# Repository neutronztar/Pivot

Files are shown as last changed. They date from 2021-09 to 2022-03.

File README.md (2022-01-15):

# Pivot
Pivot is an open source robotic art piece similar to Mark Setrakian's [Axis 1 and 2](https://www.youtube.com/watch?v=NsFBHqbNKvA&t=72s). Here is [a video](https://youtu.be/PGe4sWHx0f0) about how I designed and built it

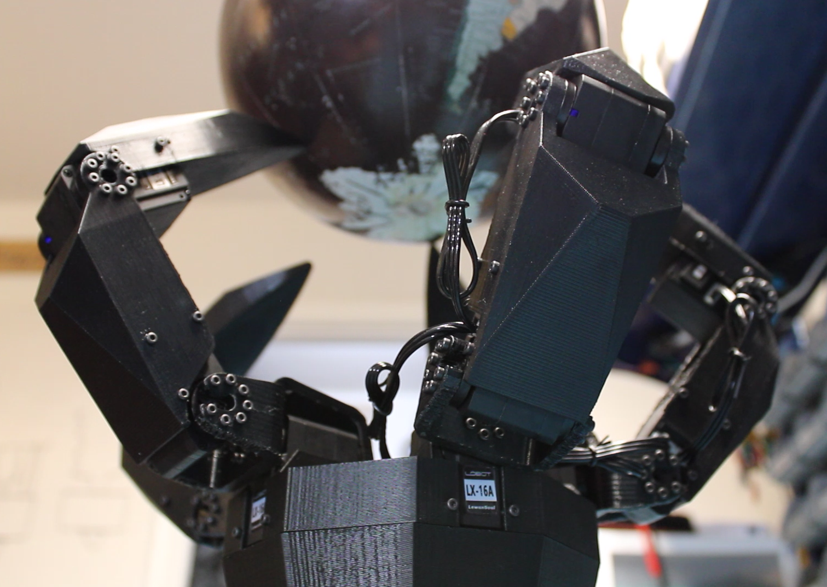
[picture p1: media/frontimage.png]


## Bill of Materials
### General Parts
| Part | Quantity | Approx Price | Total | Notes |
|---|---|---|---|---|
| [LX-16A Servo](https://smile.amazon.com/gp/product/B073XY5NT1/ref=ppx_yo_dt_b_search_asin_title?ie=UTF8&psc=1) | 15 | $20 | $300 | You also need the wires and plastic mounting rings that come with these.
| [JoyStick](https://smile.amazon.com/dp/B08CGYGMJL?psc=1&ref=ppx_yo2_dt_b_product_details) | 1 | $21 | $21 |
| [2 x 0.4 x 8 mm Machine Screws](https://www.boltdepot.com/Metric_socket_cap_Class_12.9_alloy_steel_black_oxide_finish_2mm_x_0.4mm.aspx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) | 400 | $0.0946 | $38 | Exact qty is 300, but you should get some extra. |
| [12V Power Supply](https://www.ebay.com/itm/153588427332) | 1 | $7 | $7 |
| [AC Power Connector](https://smile.amazon.com/dp/B00H8QL53A?psc=1&ref=ppx_yo2_dt_b_product_details) | 1 | $7 | $7 |
| [PETG Filament](https://smile.amazon.com/gp/product/B07PGYHYV8/ref=ppx_yo_dt_b_search_asin_title?ie=UTF8&psc=1) | 1kg | $23 | $23 |  |
| [Plaster of Paris](https://smile.amazon.com/Dap-Plaster-Paris-20-Min/dp/B008SR3W1G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) | 1 | $10 | $10 |  |
| [Round Power Switch](https://www.ebay.com/itm/203485577266?hash=item2f60af8032:g:Sh4AAOSwmDtgvNwT) | 1 | $3 | $3 |  |
| [Power Connector](https://smile.amazon.com/gp/product/B07DCXKNXQ/ref=ppx_yo_dt_b_search_asin_title?ie=UTF8&psc=1) | 1 | $7 | $7 |  |

### PCB Parts
| Part | Quantity | Approx Price | Total | Notes |
|---|---|---|---|---|
| [ESP32 DevKit](https://smile.amazon.com/gp/product/B086MLNH7N/ref=ppx_yo_dt_b_search_asin_title?ie=UTF8&psc=1) | 1 | $7 | $7 |
| [8V Buck Converter](https://smile.amazon.com/dp/B07BDDMGLG?ref=ppx_yo2_dt_b_product_details&th=1) | 1 | $7 | $7 |
| [5V Buck Converter](https://smile.amazon.com/gp/product/B01MQGMOKI/ref=ppx_yo_dt_b_search_asin_title?ie=UTF8&th=1) | 1 | $11 | $11 |
| [Molex Spox 3pin Connectors](https://www.mouser.com/ProductDetail/Molex/35301-0340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) | 5 | $0.26 | $1.30 | |
| [1000uF Electrolytic Cap](https://smile.amazon.com/dp/B06XRDWF5X?psc=1&ref=ppx_yo2_dt_b_product_details) | 4 |  | $15 |  |
| [10uF Electrolytic Cap](https://smile.amazon.com/dp/B06XRDWF5X?psc=1&ref=ppx_yo2_dt_b_product_details) | 1 | |  |  |
| [Tri-State Buffer: SN74LS241N](https://smile.amazon.com/gp/product/B08FZVPJD9/ref=ppx_yo_dt_b_search_asin_title?ie=UTF8&psc=1) | 1 | $9 | $9 |  |
| Logic Level Shifter SMD: TXS0108EPWR | 1 | |  | JLC |
| 1k Resistor SMD: 0603WAF1001T5E | 1 |  |  | JLC |
| 10k Resistor SMD: 0603WAF1002T5E | 1 |  |  | JLC |
| 100nF Cap SMD: CC0603KRX7R9BB104 | 2 |  |  | JLC |

### 3D Printed Parts
| Part | Quantity |
|---|---|
| tip.STL | 5 |
| fingerA.STL | 5 |
| knuckle.STL | 5 |
| palm.STL | 1 |
| mid.STL | 1 |
| base.STL | 1 |

#### Approximate Grand Total: $466

## The Code
To make this machine do its magic, every ".py" file in the root of the "MicroPython" directory must be uploaded to the ESP32. I used the utility ["rshell"](https://pypi.org/project/rshell/) to do this. Also the ESP32 must first be loaded with a [MicroPython binary](https://micropython.org/download/esp32/) (tested on v1.17).

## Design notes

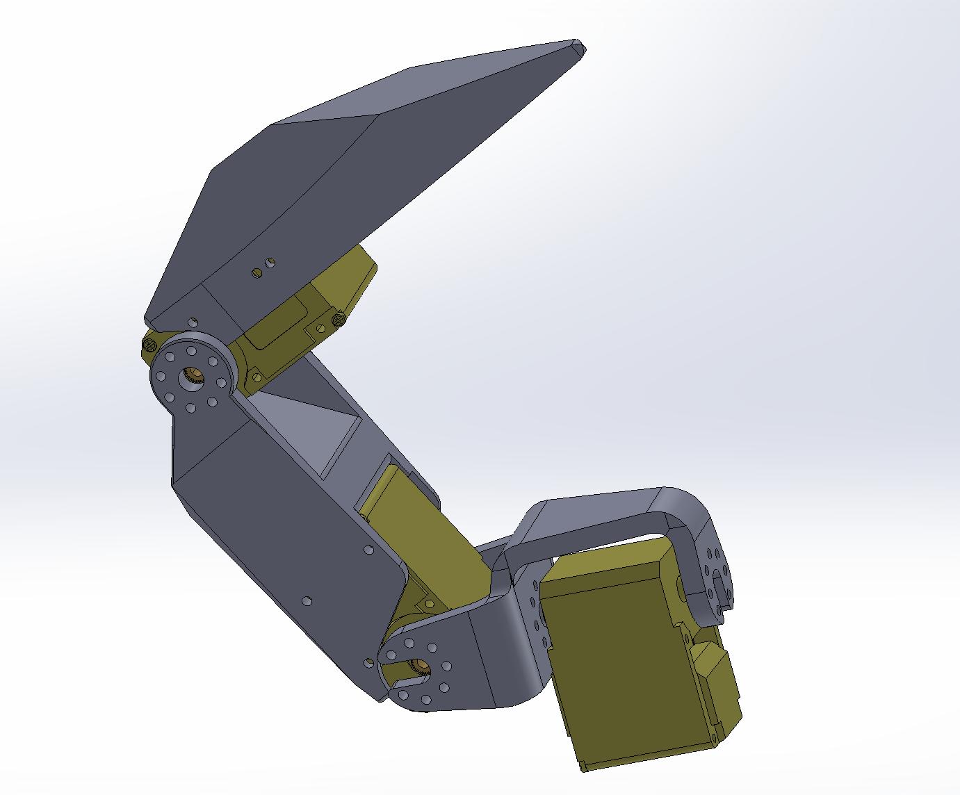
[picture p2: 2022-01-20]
media/sw_finger.jpeg

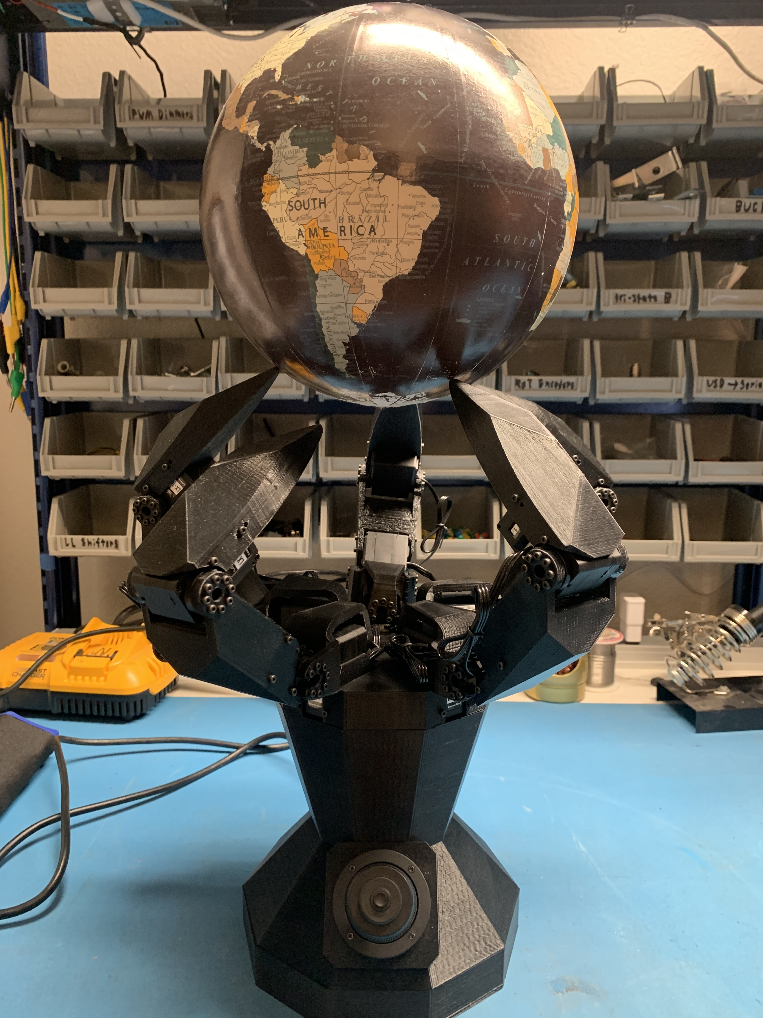
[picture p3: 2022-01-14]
media/verticalpic.jpeg

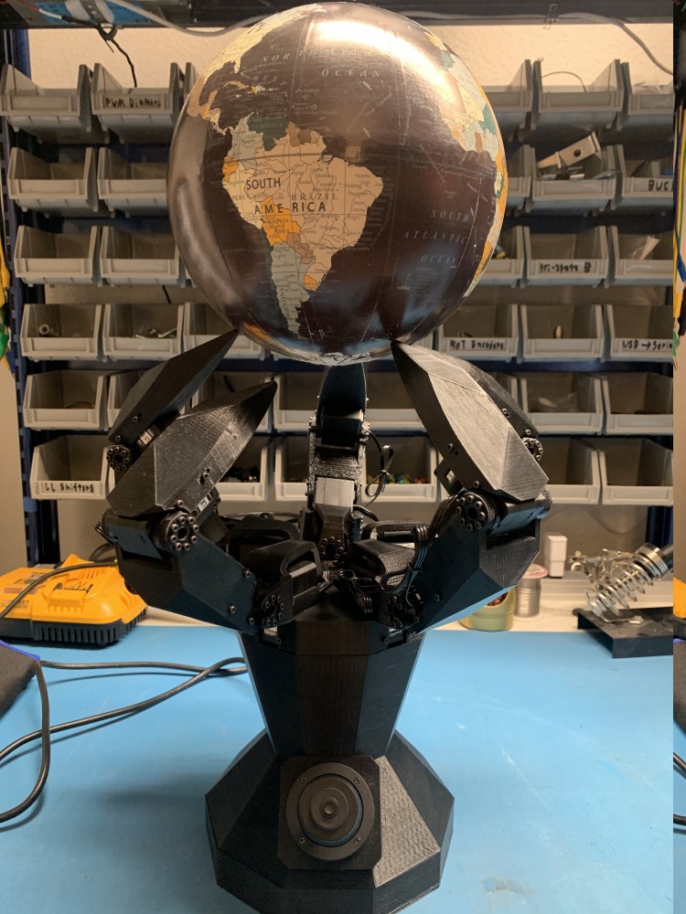
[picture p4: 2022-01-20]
media/verticalpicsmaller.jpeg

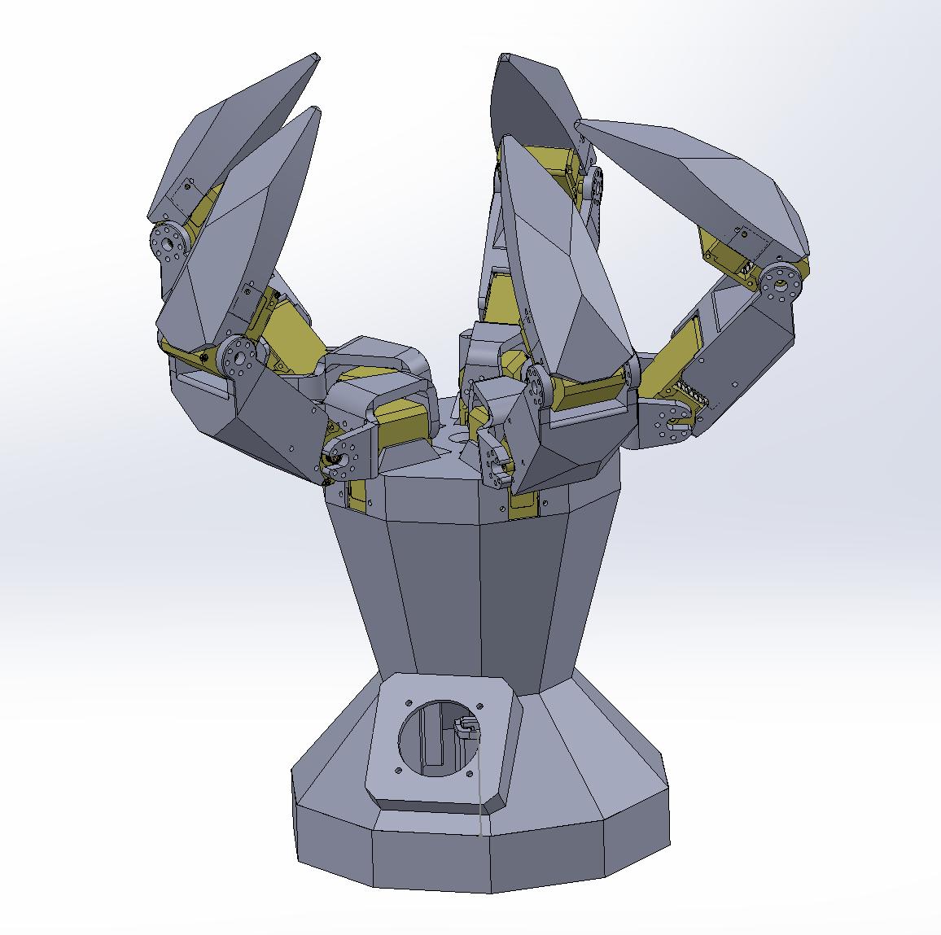
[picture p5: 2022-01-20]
media/sw.jpeg

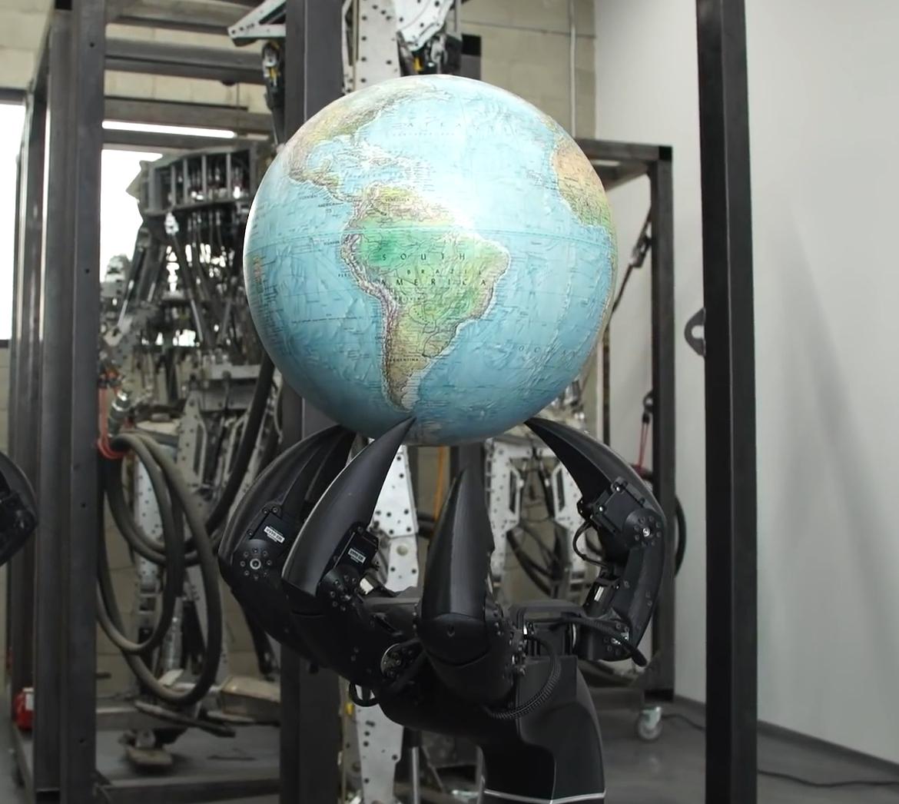
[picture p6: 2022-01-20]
media/axis.jpeg

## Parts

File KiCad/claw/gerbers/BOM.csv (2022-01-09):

Comment | Designator | Footprint | LCSC Part Number
1k | R1 | 0603 | C21190
10k | R2 | 0603 | C25804
100nF | C1,C2 | 0603 | C14663
TXS0108EPWR | U2 | TSSOP-20_4.4x6.5x0.65P | C17206

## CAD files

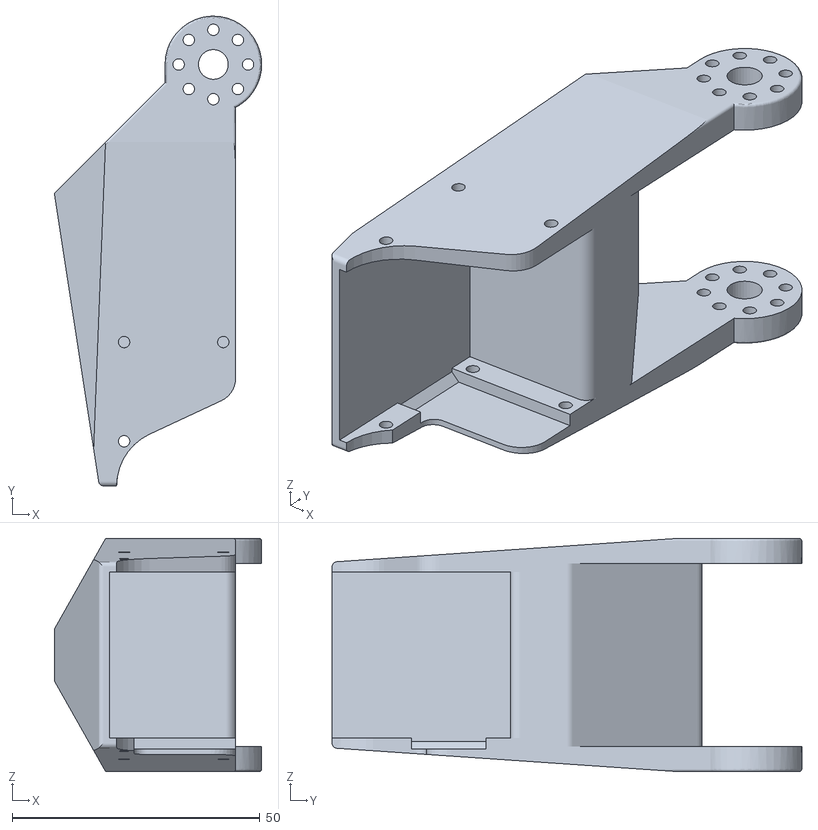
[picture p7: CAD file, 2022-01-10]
3Dmodels/fingerA.STL
41.8 x 94.7 x 47.0

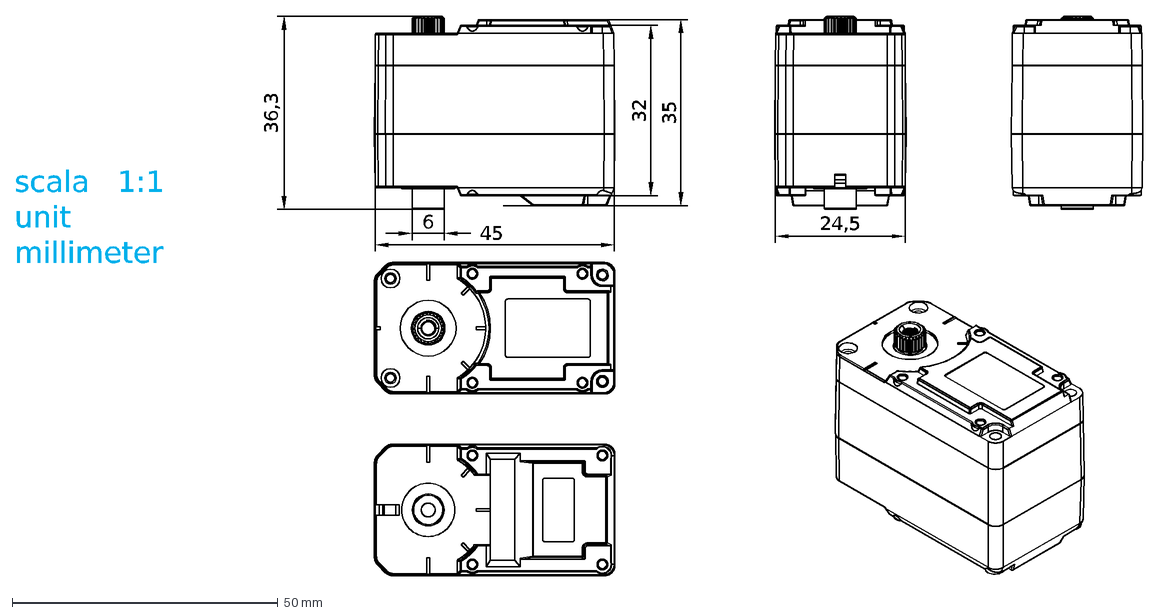
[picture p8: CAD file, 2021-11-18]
LX-16A/LX-16A.dxf
36,3
45
35
32
24,5
6
scala 1:1 unit millimeter

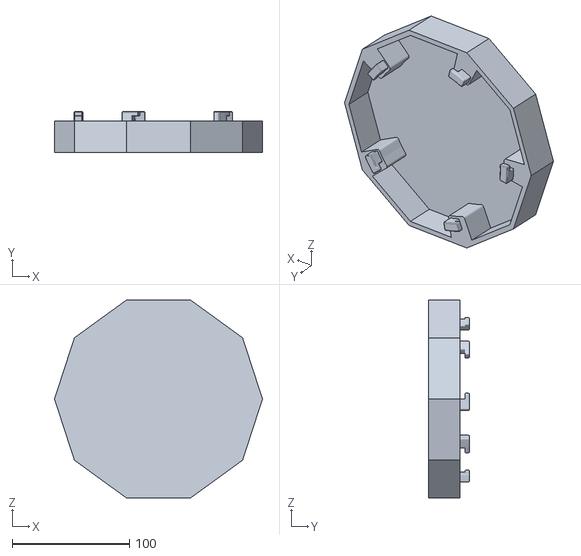
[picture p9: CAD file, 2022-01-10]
3Dmodels/base.STL
177.4 x 35.0 x 168.7

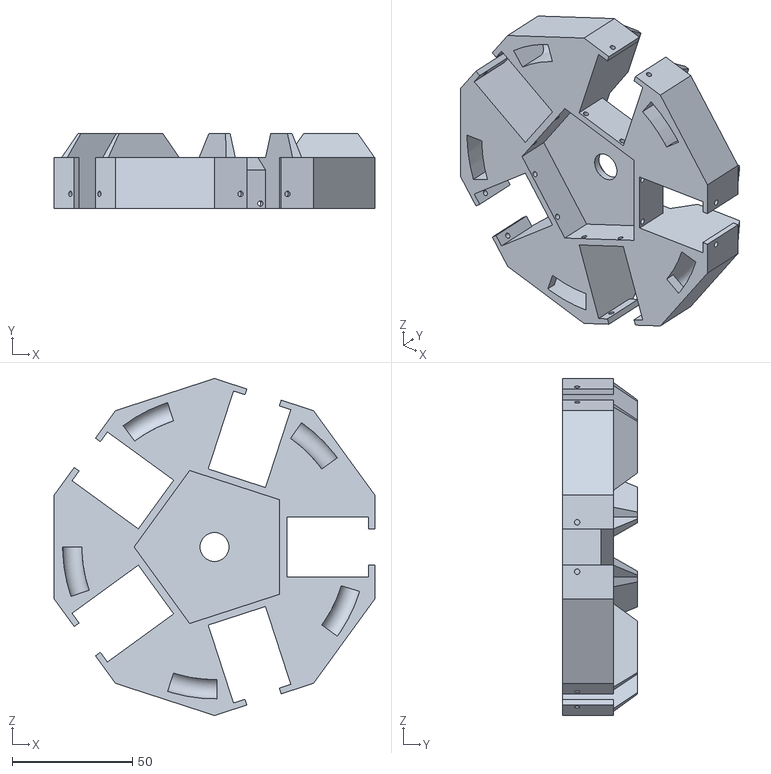
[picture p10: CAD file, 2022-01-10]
3Dmodels/palm.STL
133.0 x 31.0 x 139.8

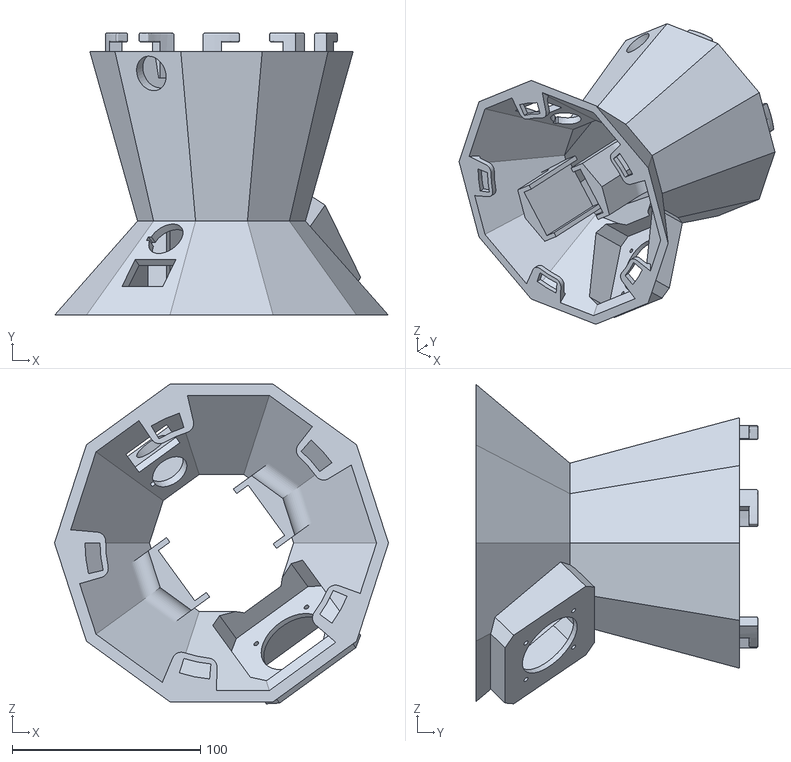
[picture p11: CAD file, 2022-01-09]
3Dmodels/mid.STL
177.4 x 150.0 x 169.8

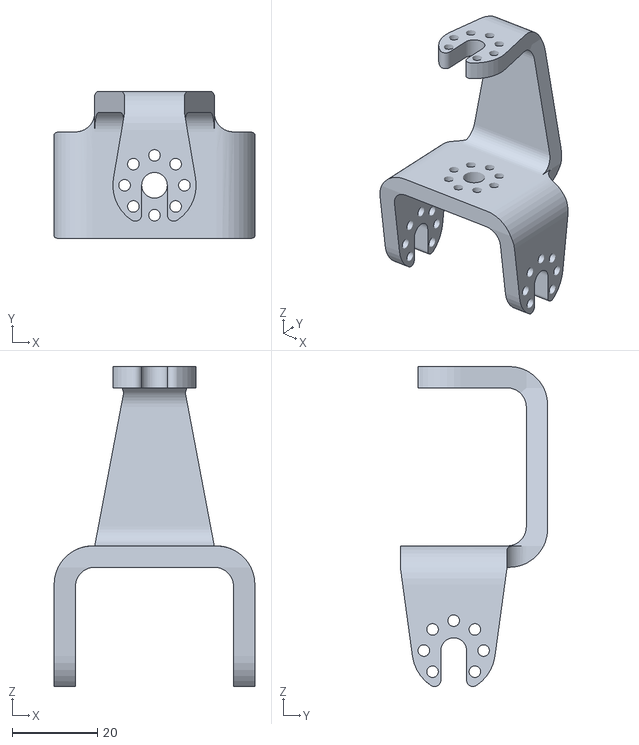
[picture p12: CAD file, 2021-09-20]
3Dmodels/knuckle.STL
47.0 x 34.5 x 74.9

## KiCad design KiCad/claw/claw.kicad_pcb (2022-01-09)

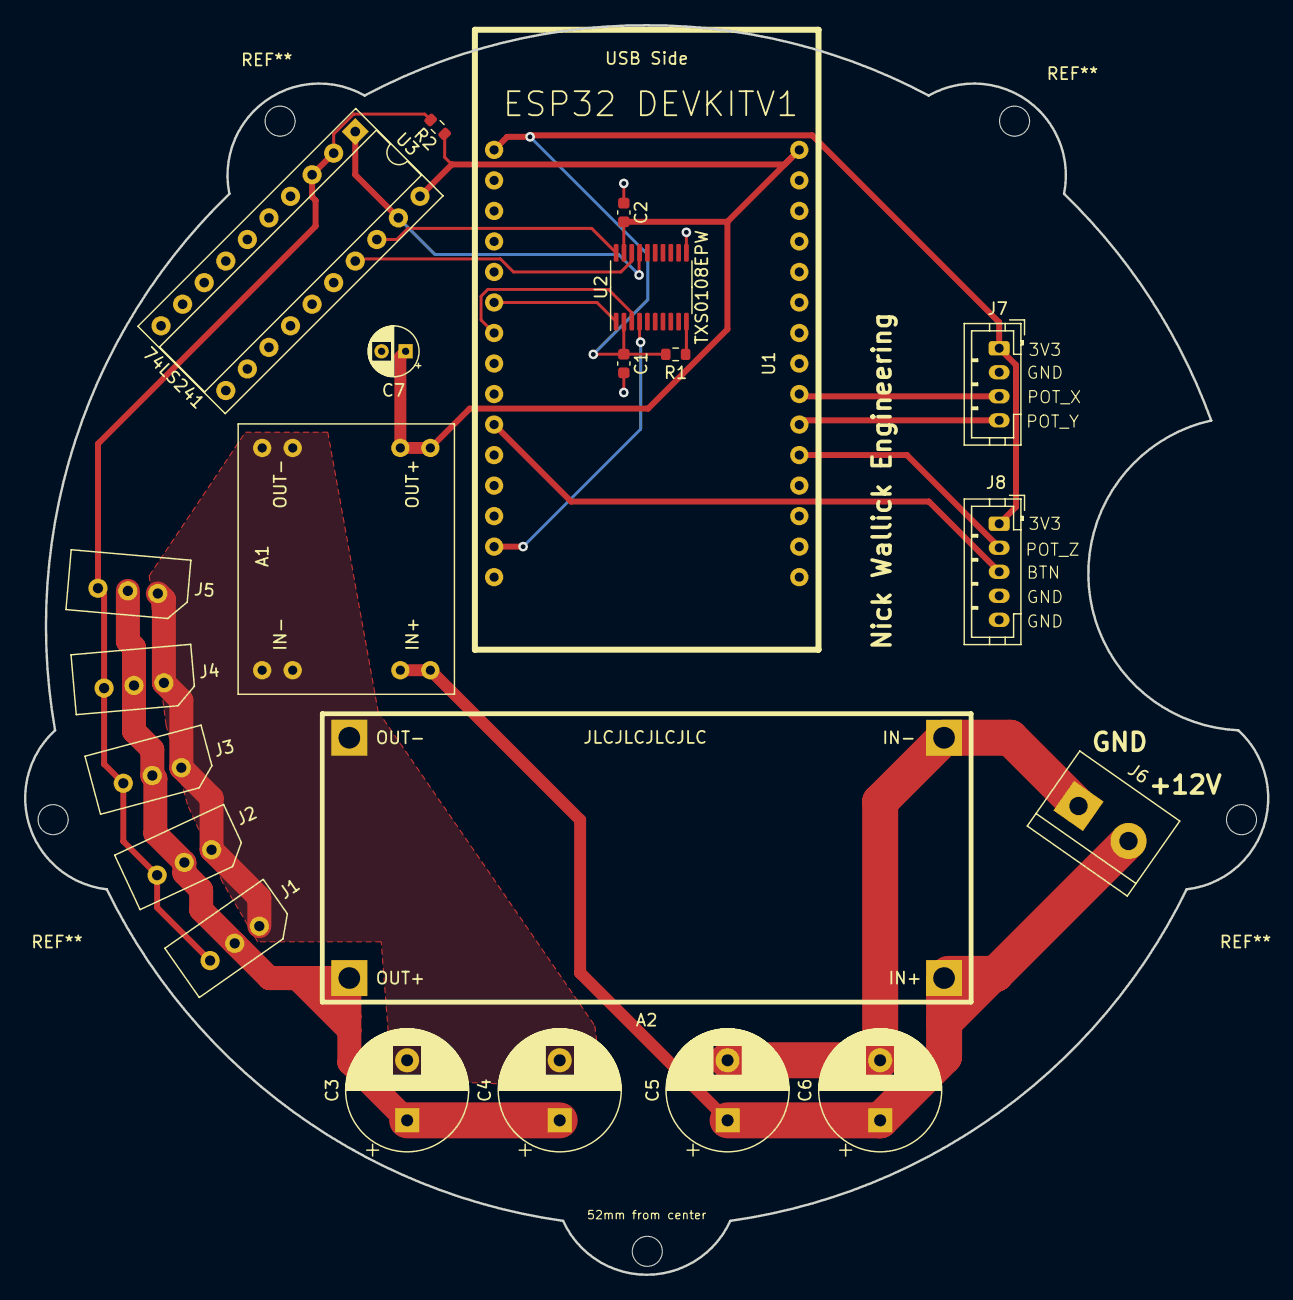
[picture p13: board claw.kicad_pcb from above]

Board: 2 copper layers, 103.5 x 104.0 mm, 22 parts (0 on the bottom side), 17 nets.

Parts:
A1: DC-DC_Buck; MP1584EN_DC-DC_Buck
A2: DC-DC_Buck; DZS_Elec_DC-DC_Buck
C1, C2: 100nF; C_0603_1608Metric
C3, C4, C5, C6: 1000u; CP_Radial_D10.0mm_P5.00mm
C7: 10u; CP_Radial_D4.0mm_P2.00mm
J1, J2, J3, J4, J5: Molex_Spox_3pin; Molex_Spox_3Pin_2.5mmPitch
J6: Screw_Terminal_01x02; TerminalBlock_bornier-2_P5.08mm
J7: Conn_01x04_Male; JST_PH_B4B-PH-K_1x04_P2.00mm_Vertical
J8: Conn_01x05_Male; JST_PH_B5B-PH-K_1x05_P2.00mm_Vertical
R1: 1k; R_0603_1608Metric
R2: 10k; R_0603_1608Metric
U1: ESP32_DEVKITV1
U2: TXS0108EPW; TSSOP-20_4.4x6.5mm_P0.65mm
U3: 74LS241; DIP-20_W7.62mm_Socket

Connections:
+3V3: C1.1, J7.1, J8.1, R1.1, U1.1, U2.2
+5V: A1.3, C2.2, C7.1, R2.1, U1.30, U2.19, U3.20
+8V: A2.3, C3.1, C4.1, J1.2, J2.2, J3.2, J4.2, J5.2
+12V: A1.4, A2.4, C5.1, C6.1, J6.2
BUTTON: J8.3, U1.10
DIR_3V3: U1.14, U2.4
DIR_5V: U2.17, U3.1, U3.19
GND: A1.1, A1.2, A2.1, A2.2, C1.2, C2.1, C3.2, C4.2, C5.2, C6.2, C7.2, J1.1, J2.1, J3.1, J4.1, J5.1, J6.1, J7.2, J8.4, J8.5, U1.2, U1.29, U2.11, U3.10
MOTOR_SIGNAL: J1.3, J2.3, J3.3, J4.3, J5.3, R2.2, U3.2, U3.3
unnamed: R1.2, U2.10
POT_X: J7.3, U1.22
POT_Y: J7.4, U1.21
POT_Z: J8.2, U1.20
RX_3V3: U1.6, U2.1
RX_5V: U2.20, U3.18
TX_3V3: U1.7, U2.3
TX_5V: U2.18, U3.17

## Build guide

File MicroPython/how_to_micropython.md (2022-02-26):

# MicroPython Commands for Controlling ESP32 on Linux #

## installing mp
cd /home/nick/.local/lib/python3.8/site-packages
python3 esptool.py --chip esp32 --port /dev/ttyUSB0 erase_flash
python3 esptool.py --chip esp32 --port /dev/ttyUSB0 --baud 460800 write_flash -z 0x1000 esp32-20210902-v1.17.bin

## list files on board
ampy -p /dev/ttyUSB0 ls

## control board with REPL
picocom /dev/ttyUSB0 -b115200
then push 'en' button on board
exit picocom with Ctrl-a --> Ctrl-x

## Connect with rshell (broken on MicroPython 1.17... or not?)
rshell -p /dev/ttyUSB0
## Then list files on board
ls /pyboard
## Enter REPL
repl
## Run file from REPL
exec(open('file.py').read())

## MicroPython Tools
ampy rshell mpfshell

## All importable modules
help('modules')

## check ram
import micropython as mp
mp.mem_info(True)

## check file-system space
import os
os.statvfs('/')
https://docs.micropython.org/en/latest/library/os.html#:~:text=file%20or%20directory.-,os.statvfs,-(path)

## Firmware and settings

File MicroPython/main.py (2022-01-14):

import time
from math import isinf, pi
from micropython import const
from machine import ADC, Pin
from claw import Claw, time_it
from constants import *


def main():
    claw = Claw(22)

    # Left and right joystick potentiometer
    potX = ADC(Pin(33))
    potX.atten(ADC.ATTN_11DB)

    # Front and back joystick potentiometer
    potY = ADC(Pin(32))
    potY.atten(ADC.ATTN_11DB)

    # Up and Down joystick potentiometer
    potZ = ADC(Pin(35))
    potZ.atten(ADC.ATTN_11DB)

    # Button on top of joystick
    button = Pin(19, Pin.IN, Pin.PULL_UP)
    button.irq(trigger=Pin.IRQ_RISING, handler=button_callback)
    global buttonPressed
    buttonPressed = False
    mode = 0

    speedTable = {
    # speed:    numFrames
      -12:        -20,       # fastest reverse
      -11:        -25,
      -10:        -30,
       -9:        -35,
       -8:        -40,
       -7:        -45,
       -6:        -50,
       -5:        -55,
       -4:        -60,
       -3:        -65,
       -2:        -70,
       -1:        -75,
        0:        -80,       # slowest reverse
        1:         80,       # slowest
        2:         75,
        3:         70,
        4:         65,
        5:         60,
        6:         55,
        7:         50,
        8:         45,
        9:         40,
        10:        35, 
        11:        30,
        12:        25,
        13:        20        # fastest
    }

    speed = -4
    numFrames = speedTable[speed]
    
    STRIDE = 1.15               # radians, must be less than 2*pi/5
    OFFSET_ANGLE = -STRIDE / 2 + pi / 10  # radians
    FRAME_TIME = const(60)      # ms
    
    center = [0, 0, 150]        # center of the circle that the finger tips move along
    radius = 50
    numFrames = -60
    phase = 0                   # sweeps 0-359
    frameStartTime = time.ticks_ms()
    firstLoop = True


    ### MAIN LOOP ###
    while True:
        # Update values based on user input
        center, radius, speed, mode = update_values(potX, potY, potZ, center, radius, speed, mode)
        numFrames = speedTable[round(speed)]
        
        # Calculate angles of all 15 servos for next frame
        angles = claw.calc_frame_angles(phase, STRIDE, OFFSET_ANGLE, radius, center)

        # ------Wait------
        while time.ticks_diff(time.ticks_ms(), frameStartTime) < FRAME_TIME:
            pass
        frameStartTime = time.ticks_ms() # reset timer
        
        # Move all fingers to frame
        claw.move_to_frame(angles, FRAME_TIME, firstLoop)
        firstLoop = False

        # Increment phase
        phase = (phase + 360 / numFrames) % 360



def update_values(potX, potY, potZ, center, radius, speed, mode):
    """Update values based on user input"""
    
    def bound(val, low, high):
        return max(low, min(high, val))
    

    # Cycle mode if button on top of joystick was pressed
    global buttonPressed
    if buttonPressed == True:
        mode = (mode + 1) % 3
        buttonPressed = False

    # Read all POTs
    joyX = potX.read() - X_AVG
    joyY = potY.read() - Y_AVG
    joyZ = potZ.read() - Z_AVG


    # Map XY joystick movement to XY globe movement
    if joyX > SLOP:
        targetX = int(min(joyX - SLOP, 1200) * 50/1200)
    elif joyX < -SLOP:
        targetX = int(max(joyX + SLOP, -1200) * 50/1200)
    else:
        targetX = 0

    if joyY > SLOP:
        targetY = int(min(joyY - SLOP, 1200) * 50/1200)
    elif joyY < -SLOP:
        targetY = int(max(joyY + SLOP, -1200) * 50/1200)
    else:
        targetY = 0

    xStep = int((targetX - center[0]) / 4)
    yStep = int((targetY - center[1]) / 4)
   
    center[0] += xStep
    center[1] += yStep

    
    if mode == 0:

        # Map spinning joystick to Z globe movement
        if joyZ > SLOP:
            zStep = int(min(joyZ - SLOP, 1200) * 6/1200)
        elif joyZ < -SLOP:
            zStep = int(max(joyZ + SLOP, -1200) * 6/1200)
        else:
            zStep = 0

        center[2] = bound(center[2] + zStep, 100, 180)
    
    elif mode == 1:

        # Map spinning joystick to radius
        if joyZ > SLOP:
            rStep = int(min(joyZ - SLOP, 1200) * 4/1200)
        elif joyZ < -SLOP:
            rStep = int(max(joyZ + SLOP, -1200) * 4/1200)
        else:
            rStep = 0
        
        radius = bound(radius + rStep, 20, 80)
    
    elif mode == 2:

        # Map spinning joystick to speed
        if joyZ > SLOP:
            speed = bound(speed - 0.2, -12, 13)
        elif joyZ < -SLOP:
            speed = bound(speed + 0.2, -12, 13)


    return center, radius, speed, mode


def button_callback(p):
    global buttonPressed
    buttonPressed = True


if __name__ == "__main__":
    main()

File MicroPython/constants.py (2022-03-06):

from math import radians, sin, cos
from micropython import const


# Distance from center of palm to axis 1 for each finger
D = (91, 91, 91, 91, 91)

# Angle from X-axis for each finger
THETA_DEG = (18, 90, 162, 234, 306)
THETA = tuple(map(radians, THETA_DEG))

# Vector for each of the finger start positions
D_VECT = (
    (D[0]*cos(THETA[0]), D[0]*sin(THETA[0]), 0),
    (D[1]*cos(THETA[1]), D[1]*sin(THETA[1]), 0),
    (D[2]*cos(THETA[2]), D[2]*sin(THETA[2]), 0),
    (D[3]*cos(THETA[3]), D[3]*sin(THETA[3]), 0),
    (D[4]*cos(THETA[4]), D[4]*sin(THETA[4]), 0)
)

# Lengths (mm)
FINGER_LEN = const(85) # exact: 85.38
TIP_LEN = const(118)   # exact: 118.04

# Motor IDs (knuckle,finger,tip) for each finger
MOTOR_ID = ((0,1,2), (3,4,5), (6,7,8), (9,10,11), (12,13,14))

# Offest Angles (knuckle,finger,tip) for each finger
OFFSET_ANGLE = ((-1,-2,9), (1,-2,9), (-1,-6,9), (1,-4,6), (-1,-6,10))

# Motor angle limits - limits move with the offsets!
KNUCKLE_LIMIT = (45, 135)
FINGER_LIMIT = (0, 114)
TIP_LIMIT = (0, 133)

# Joystick potentiometer middle positions
X_AVG = 1690
Y_AVG = 1678
Z_AVG = 1720
SLOP = 300 # Distance from middle position before something starts happening

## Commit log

2021-09-20 added knuckle.stl
    [knuckle.STL]
2021-09-20 added motor step and knuckle step
    [Lewansoul LX-16A Servo.stp, knuckle.STEP]
2021-09-20 added palm
    [palm.FCStd]
2021-09-21 created palm prototype and messed around with assemblies
    [assembly4.FCStd, knuckle.FCStd, palm.FCStd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]
2021-09-21 added freecad practice folder
    [pipeflange.FCStd]
2021-09-22 fixed problem connecting palm to servos in assembly4
    [AssemblyFile.FCStd, Bague.fcstd, Bielle.FCStd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]
2021-09-23 started natural version of palm and added sliced folder
    [AA8_knuckle.3mf, assembly4.FCStd, knuckle.FCStd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]
2021-09-28 worked on fingerA
    [bodyPractice.FCStd, fingerA.FCStd, fingerAv2.FCStd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]
2021-11-13 did some things
    [AA8_knuckle.3mf, AA8_left.3mf, AA8_tip.3mf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]
2021-11-18 created test files for controlling motors
    [Bottom Bracket.dxf, LX-16A.dxf, LXD16 v1.f3d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]
2021-11-19 started 3d motor angle calculation
2021-11-25 set offsets for all fingers and restructured functions to be in claw object
2021-11-26 added validate() for validating results from servos
2021-11-27 restructured lx16.py and added query_motors() to claw.py
2021-12-04 added files for reading rotary encoders
2021-12-04 moved main loop to "main.py" and kept supporting functins in "claw.py"
2021-12-16 added new sliced files
    [AA8_mid.3mf, AA8_palm.3mf]
2021-12-16 ditched rotary encoders and added joystick control
2021-12-17 cleaned up repo and added KiCAD circuitboard data
    [AssemblyFile.FCStd, Bague.fcstd, Bielle.FCStd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]
2021-12-18 added joystick connectors to schematic and layed out components on pcb
    [claw.kicad_pcb, claw.sch]
2021-12-18 pcb traces
    [claw.kicad_pcb, claw.sch]
2021-12-18 added PCB mounting holes
    [claw.kicad_pcb]
2022-01-09 updated finger offsets
    [AA8_knuckle.3mf, AA8_left.3mf, AA8_mid.3mf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]
2022-01-10 added all 3D models
    [Lewansoul LX-16A Servo.stp, base.STL, fingerA.STL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]
2022-01-12 started BOM
2022-01-14 updated BOM and added /media
2022-01-22 kicad update
